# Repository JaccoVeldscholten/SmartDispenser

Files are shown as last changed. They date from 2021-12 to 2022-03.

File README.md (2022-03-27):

<div align="center">
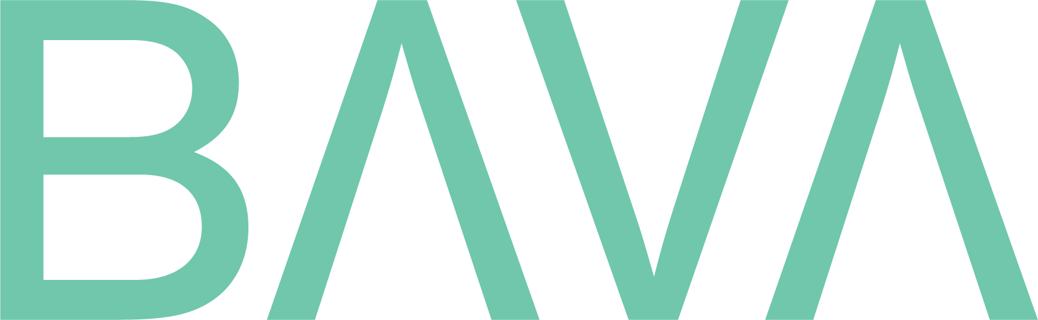
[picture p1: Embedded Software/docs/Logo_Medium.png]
  
</div>


![Build with PlatformIO](https://img.shields.io/badge/build%20with-PlatformIO-orange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)

# BAVA SmartDispenser 

Smart Dispenser is a device that has been developed to measure the odor in a toilet. If the smell of the toilet is of poor quality, a diffuser will be activated to dispel or mask the bad smell.

Measuring stench is done by a TVOC sensor. Furthermore, information is collected such as the temperature, moisture and how much the toilet is used.

## Installation

#### Windows (Tested on Windows 11)
* [Visual Code](https://code.visualstudio.com/) as IDE 
* [PlatformIO for code](https://platformio.org/install/ide?install=vscode) as extension for building on ESP32
* [SolidWorks](https://www.solidworks.com/) for editing the housing

After installing these tools the project can be pulled from GitHub and opened in VSCode and compiled & flashed with PlatformIO

## Usage / compiling
Please refer to [instructions](https://docs.platformio.org/en/latest/core/quickstart.html) of PlatformIO

For adjusting standard data see the chapter configuration.

## Configuration & Enviroment Variables
Many settings can be adjusted via the file config.h. Here are the WiFi settings and more relevant values.

It is also possible to set the threshold here when the sensor should be activated. The average value in a toilet is indicated in the table below. Certain values may differ per toilet. These are therefore adjustable in the configuration file.

| Measurement Value | No Lingering smell | Middle Lingering smell  | No Lingering smell | 
| :---: | :-: | :-: | :-: |
| TVOC PPM | 0 | 10 | > 10
| TVOC CO2 | 150 | 250 | > 250

More information and access to sample data can be seen in the Google Colab.

***Config.h***
````
/* WiFi Settings */
#define WIFI_SSID                       "TestSSID"
#define WIFI_PASSWORD                   "TestPassword!"

/* Defines the Min/Max Treshold of Stench in TVOC value */
#define TRESHOLD_PPM_MIN                3
#define TRESHOLD_PPM_MAX                5

/* Defines the Min/Max Treshold of Stench in CO2 value */
#define TRESHOLD_CO2_MIN                200
#define TRESHOLD_CO2_MAX                500

/* Measurement Interval */
#define TIME_TO_SLEEP          60     /* Time Device will go to sleep (in seconds) */            
#define TIME_TO_SLEEP_RECHECK  60     /* Time Device will go to sleep (in seconds) before recheck if someone left the toilet */
````

## Circuit Board
In order to combine the product into one product, it was decided to develop a printed circuit board containing the required sensors on board. Also, the microcontroller is soldered to the printed circuit board. More documentation about this object can be found at ....

## 3D Model & Assembly
The entire product is drawn in SolidWorks. The drawing files are included in this GitHub. A simple but handy model was taken into account because the model had to be printed with a 3D printer.

## Testing
The product has been extensively tested by data analyzes and used traceability matrixses to test the product. The results are included in this repo.

## Documentation in depth
Use the DoxyGen Folder for documentation.
For Writing Documentation use the following link: 

## License
MIT

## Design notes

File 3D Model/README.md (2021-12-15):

<div align="center">
  
</div>

# 3D Design & Assembly
To assemble the product, this page has been prepared for the developer or production employee to assemble the product together.

# Build instructions
***UNDER CONSTRUCTION**: This section will include:*
- *Bill of Materials*
- *Mechanical assembly instructions*
- *Electronics/Wiring instructions*

---

## Bill of materials
### 3D Printable
3D Printable files are found in [/CAD/3D Models (To Print)](../STL)
- [Base](../STL/Base.STL)
- [Backplate](../STL/Base.STL)
- [Battery Box](../STL/Base.STL)
- [Water Compartment](../STL/Base.STL)

*Optional*
- [Logo](../STL/Base.STL)
- [Box Design](../STL/Base.STL)
### Non 3D Printable
Some parts such as the mechanical parts or electrical parts cannot be printed. These must be purchased. The printed circuit board can be developed yourself. Read the Circuit Board section for this. The purchase of the printed circuit board can be done at BAVA Solutions.

### Electronic components
- **Circuit Board** Provider by BAVA Solutions (Or see Circuit Board Section)
- **TVOC Sensor** Sensor CCS811
- **Temperature Sensor** Bosch BME280 
- **Battery** 1S LiPo Aprox 3200 mAh

### Mechanical components
- **1x** Hot Glue Gun with sticks 

---

# Mechanical assembly

### Step 1: Print the base element
push fit the bearings and secure with a nut and bolt Push fit bearings

  The first step of assembly is to print the [base](../STL/Base.stl) element of the product. From this object it is possible to connect the rest of the elements.
  Print the basic element and lay it flat on the table with the open cloth outwards.<br><br><br><br><br><br><br><br><br>

---

### Step 2: Insert the water compartment 
push fit the bearings and secure with a nut and bolt Push fit bearings

  The first step of assembly is to print the [base](../STL/Base.stl) element of the product. From this object it is possible to connect the rest of the elements.
  Print the basic element and lay it flat on the table with the open cloth outwards.

---

### Step 3: Insert the sensors
push fit the bearings and secure with a nut and bolt Push fit bearings

  The first step of assembly is to print the [base](../STL/Base.stl) element of the product. From this object it is possible to connect the rest of the elements.
  Print the basic element and lay it flat on the table with the open cloth outwards.

---

### Step 4: Inert the circuit board
push fit the bearings and secure with a nut and bolt Push fit bearings

  The first step of assembly is to print the [base](../STL/Base.stl) element of the product. From this object it is possible to connect the rest of the elements.
  Print the basic element and lay it flat on the table with the open cloth outwards.

---

### Step 5: Connect the wires
push fit the bearings and secure with a nut and bolt Push fit bearings

  The first step of assembly is to print the [base](../STL/Base.stl) element of the product. From this object it is possible to connect the rest of the elements.
  Print the basic element and lay it flat on the table with the open cloth outwards.

---

### Step 6: Insert the battery
push fit the bearings and secure with a nut and bolt Push fit bearings

  The first step of assembly is to print the [base](../STL/Base.stl) element of the product. From this object it is possible to connect the rest of the elements.
  Print the basic element and lay it flat on the table with the open cloth outwards.

---

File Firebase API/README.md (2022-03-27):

## Index

[Overview API](#overview-api)

[Run Locally](#run-locally)

[Documentation](#documentation)

- ###### [AddDevice](#adddevice-1)
- ###### [AddDeviceData](#adddevicedata-1)
- ###### [AddLocation](#addlocation-1)
- ###### [GetAllBuildings](#getallbuildings-1)
- ###### [GetDeviceStatusPerBuilding](#getdevicestatusperbuilding-1)
- ###### [GetLogsOfADevice](#getlogsofadevice-1)
- ###### [GetStatsOfADevice](#getstatsofadevice-1)
- ###### [RemoveDevice](#removedevice-1)
- ###### [RemoveLocation](#removelocation-1)

[Deployment](#deployment)

[FAQ](#faq)

## Overview API

The API is hosted on Firebase functions. We choose for Firebase because we can also use Firebase Firestore as our document-based-database. Besides you pay for what you use. So if you don’t have a lot of customers you will not do a lot of requests to Firebase which means the costs for the API will also be low. As you can see in the image below there is even a free quota. So for development we don’t

With this API you can interact with the data which is generated by the smart dispensers.
You can also use our app which has the API integrated.

## Run Locally

Clone the project

```bash
  git clone git@gitlab.com:bava-solutions/bava-solutions-api.git
```

Go to the project directory

```bash
  cd bava-solutions-api
```

Install dependencies

```bash
  cd functions
  npm install
  npm install firebase-tools -g
  npm install nodemon -g
```

Start the server

```bash
  cd functions (if youre not already there)
  nodemon -e ts --exec "npm run serve"
```

## Documentation

In production environment the url for the api is "https://us-central1-bava-solutions.cloudfunctions.net/"
In development environment the url for the api is "http://localhost:5001/bava-solutions/us-central1/"

### AddDevice

POST `url/AddDevice`

| **Parameter** | **Type** | **Explanation** |
| --- | --- | --- |
| building | String | The name of the building you want to add. |
| gender | Number | 0 = both genders. 1 = male. 2 = female. |
| name | String | This is the name of the smartdispenser. |
| mac | String | This is the macaddress of the smartdispenser. |
| description | String | This is a description of the smartdispenser. |
| location | String | The location where the smartdispenser is located. |

Possible return code with data
```
StatusCode 315:
    "Please send a POST request"
StatusCode 404:
    "No building found with the name of {building}"
StatusCode 400:
{
    "err": error
}
StatusCode 200:
    "Device succesfully added!"
```

### AddDeviceData

POST `url/AddDeviceData`

| **Parameter** | **Type** | **Explanation** |
| --- | --- | --- |
| tvoc\_ppm | Number | This is the measured air quality |
| tvoc\_co2 | Number | This is the meusured CO2 that’s in the air |
| temp | Number | This is the temperature that the sensor of the smart dispenser measures. |
| hum | Number | This is the humidity that is measured |
| occupied | Boolean  | This variable will be true if someone is using the toilet. If the toilet is not occupied it will be false. |
| mac | String | This is the mac-address of the smart dispenser. |
| pressure | Number | This is the measured pressure in the air. |
| altitude | Number | This will be submitted because we want to check if the altitude has some impact on the other values. |
| liquidLevel | Number | This is a percentage of the amount of liquid left in the smartdispenser. |
| batteryLevel  | Number | This is a percentage of energy still left in the battery. |

Possible return codes with data
```
StatusCode 315:
    "Please send a POST request"
StatusCode 400:
{
    "err": error
}
StatusCode 400:
{
    "Temperature too high. Log aborted"
}
StatusCode 200:
    "Sensordata successful submitted"
```

### AddLocation

POST `url/AddLocation`

| **Parameter** | **Type** | **Explanation** |
| --- | --- | --- |
| buildingName  | String | This is the name of the building you want to add |
| companyName | String | This is the company of the building |
| address | String | This is the address of the building |

Possible return codes with data
```
StatusCode 315:
    "Please send a POST request"
StatusCode 400:
{
    "err": error
}
StatusCode 200:
    "Location successful added"
```

### GetAllBuildings

GET `url/GetAllBuildings`

Possible return code with data
```
StatusCode 400:
{
    "err": error
}
StatusCode 200:
[
    "Chef",
    "Fokke",
    "Hanz",
    "BuildingGoogle"
]

```

### GetDeviceStatusPerBuilding

in the place of `MACADDRES` you need to put the macaddress

GET `url/GetDeviceStatusPerBuilding/MACADDRES`

Possible return code with data
```
StatusCode 404:
    "No building found with the name of {BUILDING}"
StatusCode 404:
    "No devices connected to building {BUILDING}"
StatusCode 400:
{
    "err": error
}
StatusCode 200:
[
  {
    "mac": "F0:08:D1:D8:07:D4",
    "altitude": 142,
    "tvoc_ppm": 8,
    "tvoc_co2": 198,
    "liquidLevel": 100,
    "timestamp": {
      "_seconds": 1638423192,
      "_nanoseconds": 216000000
    },
    "pressure": 99682,
    "hum": 36,
    "batteryLevel": 100,
    "occupied": true,
    "temp": 19,
    "name": "real device",
    "location": "Jacco WC",
    "description": "pls dont delete",
    "gender": 0
  }
]
```

### GetLogsOfADevice

in the place of `MACADDRES` you need to put the macaddress

GET `url/GetLogsOfADevice/MACADDRES`

Possible return code with data
```
StatusCode 400:
{
    "err": error
}
StatusCode 200:
[
  {
    "tvoc_co2": 0,
    "hum": 40,
    "batteryLevel": 100,
    "occupied": true,
    "temp": 23,
    "liquidLevel": 100,
    "timestamp": {
      "_seconds": 1638397086,
      "_nanoseconds": 712000000
    },
    "altitude": 160,
    "pressure": 99477,
    "mac": "F0:08:D1:D8:07:D4",
    "tvoc_ppm": 0
  },
  {
    "tvoc_co2": 179,
    "batteryLevel": 100,
    "hum": 40,
    "mac": "F0:08:D1:D8:07:D4",
    "temp": 23,
    "timestamp": {
      "_seconds": 1638397235,
      "_nanoseconds": 972000000
    },
    "pressure": 99480,
    "altitude": 160,
    "liquidLevel": 100,
    "tvoc_ppm": 5,
    "occupied": true
  }
]
```

### GetStatsOfADevice

in the place of `MACADDRES` you need to put the macaddress

GET `url/GetStatsOfADevice/MACADDRES`

Possible return code with data
```
StatusCode 400:
{
    "err": error
}
StatusCode 200:
{
    "TotalVisitors": {
    "01/12/2021": 7,
    "02/12/2021": 58,
    "03/12/2021": 29
    },
    "AverageTemperature": {
    "01/12/2021": 22.04,
    "02/12/2021": 21.589041095890412,
    "03/12/2021": 18.8796992481203
    },
    "AverageHumidity": {
    "01/12/2021": 39.28,
    "02/12/2021": 32.10502283105023,
    "03/12/2021": 30.60902255639098
    },
    "Last100MeasuredPPM": {
    "01:42": 6,
    "01:47": 8,
    "01:52": 7,
    "01:57": 7,
    }
}
```

### RemoveDevice

POST `api/RemoveDevice`

| **Parameter** | **Type** | **Explanation** |
| --- | --- | --- |
| building | String | The name of the building you want to delete.  |
| mac | String | This is the macaddress of the smartdispenser. |

Possible return code with data
```
StatusCode 315:
    "Please send a POST request"
StatusCode 404:
    "No building found with the name of {building}"
StatusCode 400:
{
    "err": error
}
StatusCode 200:
    "Device succesfully removed!"
```

### RemoveLocation

POST `url/RemoveLocation`

| **Parameter** | **Type** | **Explanation** |
| --- | --- | --- |
| buildingName  | String | The name of the building you want to delete |

Possible return code with data
```
StatusCode 315:
    "Please send a POST request"
StatusCode 400:
{
    "err": error
}
StatusCode 200:
    "Gebouw {buildingName} verwijderd"

```
## Deployment

To deploy this project run the following commands inside your project directory

```bash
  cd functions
  npm run deploy
```

## FAQ

#### How do I use this API?

You can call the endpoints from the production environment.
There is also an example app with implementation for the API available on our Git.

#### Is the API free to use?

Yes, however in the future there might be some new functions which will be hidden behind a paywall

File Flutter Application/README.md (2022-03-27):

# bava

A new Flutter project.

## Getting Started

FlutterFlow projects are built to run on the Flutter _stable_ release.

### IMPORTANT:

For projects with Firestore integration, you must first run the following commands to ensure the project compiles:

```
flutter pub get
flutter packages pub run build_runner build --delete-conflicting-outputs
```

This command creates the generated files that parse each Record from Firestore into a schema object.

### Getting started continued:

This project is a starting point for a Flutter application.

A few resources to get you started if this is your first Flutter project:

- [Lab: Write your first Flutter app](https://flutter.dev/docs/get-started/codelab)
- [Cookbook: Useful Flutter samples](https://flutter.dev/docs/cookbook)

For help getting started with Flutter, view our
[online documentation](https://flutter.dev/docs), which offers tutorials,
samples, guidance on mobile development, and a full API reference.

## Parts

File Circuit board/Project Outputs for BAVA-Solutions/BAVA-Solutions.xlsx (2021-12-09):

Comment | Description | Designator | Footprint | LibRef | Quantity
10uF | Chip Multilayer Ceramic Capacitors for General Purpose, 0603, 10uF, X5R, 15%, 20%, 6.3V | C1, C2, C8 | FP-GRM188-0_1-e0_2_0_55-IPC_C | CMP-2006-02792-2 | 3
100nF | Chip Capacitor, 0.1 uF, +/- 10%, 50 V, -55 to 125 degC, 0603 (1608 Metric), RoHS, Tape and Reel | C3, C4, C5, C6, C7 | CAPC1608X90X35ML10T15 | CMP-2100-03643-1 | 5
BAT54HT1G | Schottky Barrier Diode, 2-Pin SOD-323, Pb-Free, Tape and Reel | D1 | ONSC-SOD-323-2-477-02_V | CMP-1055-00462-1 | 1
B2B-XH-A(LF)(SN) | CONN HEADER VERT 2POS 2.5MM | J1, J4 | FP-B2B-XH-A_LF_SN-MFG | CMP-2000-05888-3 | 2
B3B-XH-A(LF)(SN) | CONN HEADER VERT 3POS 2.5MM | J2, J5 | FP-B3B-XH-A_LF_SN-MFG | CMP-17439-000014-2 | 2
629105150921 | Micro USB 2.0 Type AB Receptacle WR-COM, Horizontal, SMT | J3 | 629105150921 | CMP-1502-03249-1 | 1
S6B-XH-A-1(LF)(SN) | CONN HEADER R/A P6OS 2.5MM | J? | FP-S6B-XH-A-1_LF_SN-MFG | CMP-17439-000023-1 | 1
ESP32-WROOM-32D | WIFI MODULE 32MBITS SPI FLASH | MD1 | FP-ESP32-WROOM-32D-MFG | CMP-194065-000003-1 | 1
61301011121 | THT Vertical Pin Header WR-PHD, Pitch 2.54 mm, Single Row, 10 pins | P1 | 61301011121 | CMP-1502-01082-1 | 1
NPN | High Voltage Transistor, NPN Silicon, 3-Pin SOT-23, Pb-Free, Tape and Reel | Q1, Q2 | ONSC-SOT-23-3-318-08_V | CMP-1048-00662-1 | 2
MMBT2222ALT1G | General Purpose Transistor, NPN Silicon, 3-Pin SOT-23, Pb-Free, Tape and Reel | Q3 | ONSC-SOT-23-3-318-08_V | CMP-1048-00538-1 | 1
10K | Chip Resistor, 10 KOhm, +/- 1%, 0.1 W, -55 to 155 degC, 0603 (1608 Metric), RoHS, Tape and Reel | R1, R4, R5, R6, R7, R8, R11 | RESC1609X55X30LL15T15 | CMP-1012-00623-3 | 7
470 | Chip Resistor, 10 KOhm, +/- 1%, 0.1 W, -55 to 155 degC, 0603 (1608 Metric), RoHS, Tape and Reel | R2, R3 | RESC1609X55X30LL15T15 | CMP-1012-00623-3 | 2
1K | Chip Resistor, 10 KOhm, +/- 1%, 0.1 W, -55 to 155 degC, 0603 (1608 Metric), RoHS, Tape and Reel | R10 | RESC1609X55X30LL15T15 | CMP-1012-00623-3 | 1
1571527-2 | SWITCH TACTILE SPST-NO 0.05A 24V | SW1, SW2 | FP-1571527-2-MFG | CMP-03402-000033-1 | 2
TC1262-3.3VDBTR | 500mA Fixed Output CMOS LDO, 3-Pin SOT-223, Extended Temperature, Tape and Reel | U1 | SOT-223-DB3_L | CMP-0136-00481-1 | 1
CH340C | USB to serial chip CH340 | U2 | SO016 | CH340C | 1
BME280 | SENSOR PRESSURE HUMIDITY TEMP | U3 | FP-BME280-MFG | CMP-2000-05073-3 | 1
1655 | Intelligent Control LED Integrated Light Source, 3.5 to 5.3 V, -25 to 80 degC, 4-Pin SMD, RoHS, Tape and Reel | U4 | ADA-RGB-1655_V | CMP-2000-05026-1 | 1

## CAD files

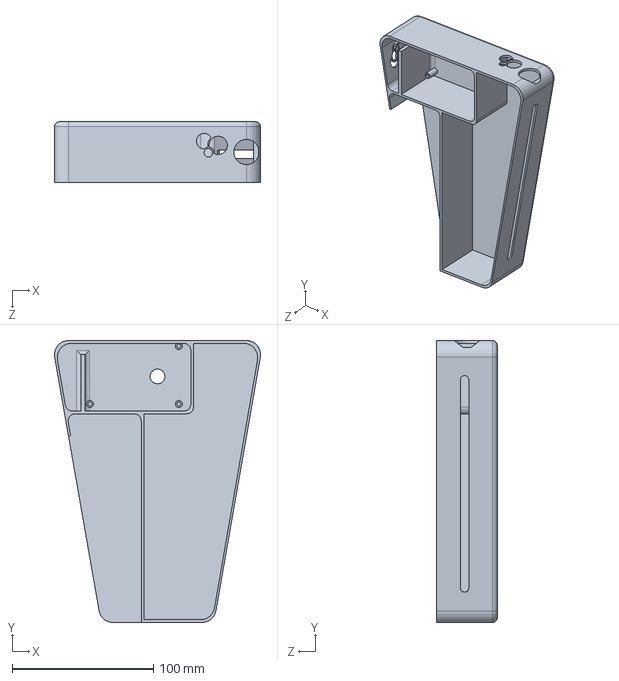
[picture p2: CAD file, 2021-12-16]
3D Model/New_front.SLDPRT
146.1 x 200.0 x 43.0 mm

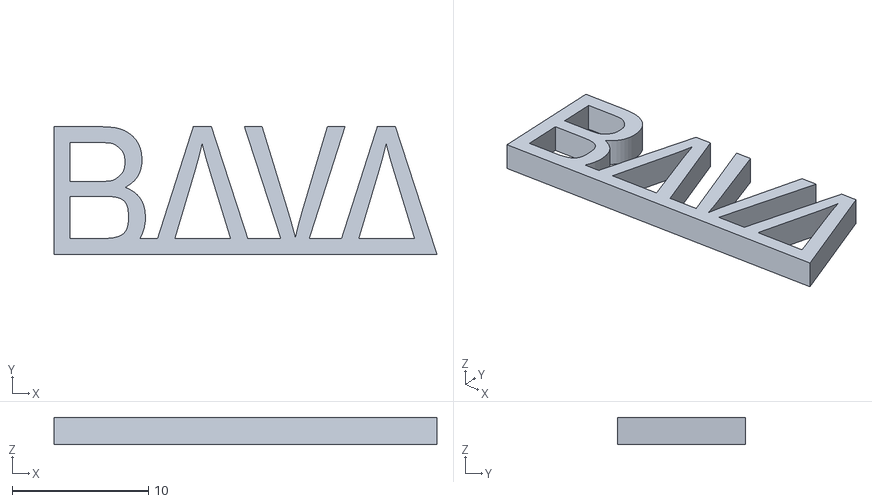
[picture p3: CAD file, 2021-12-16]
3D Model/STL/Logo.STL
28.1 x 9.36 x 2.00

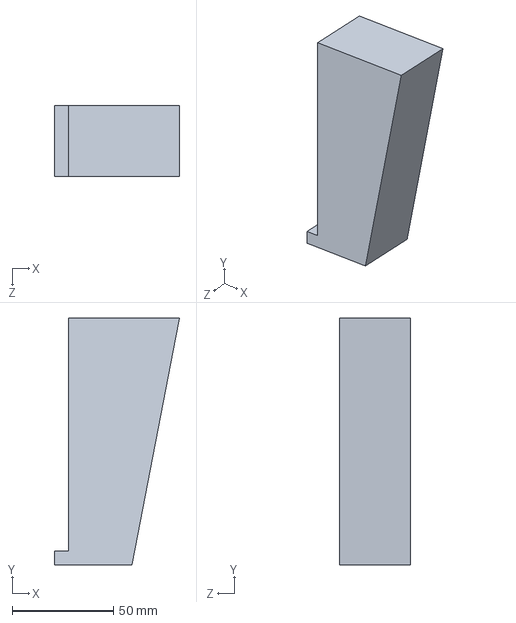
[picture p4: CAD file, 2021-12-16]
3D Model/Real_Water.SLDPRT
61.8 x 122.0 x 35.0 mm

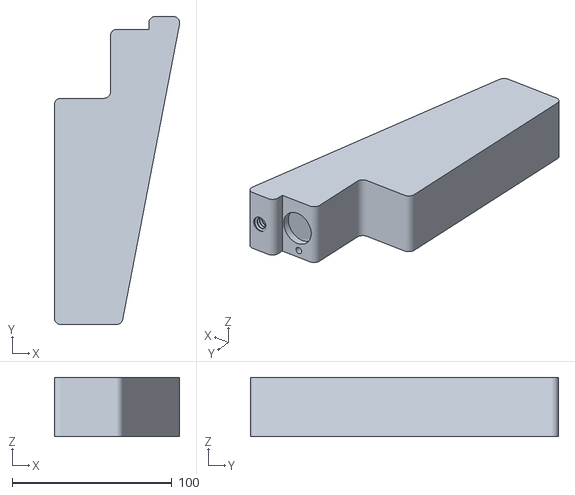
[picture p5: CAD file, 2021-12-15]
3D Model/STL/Water Compartment.STL
78.6 x 193.0 x 37.0

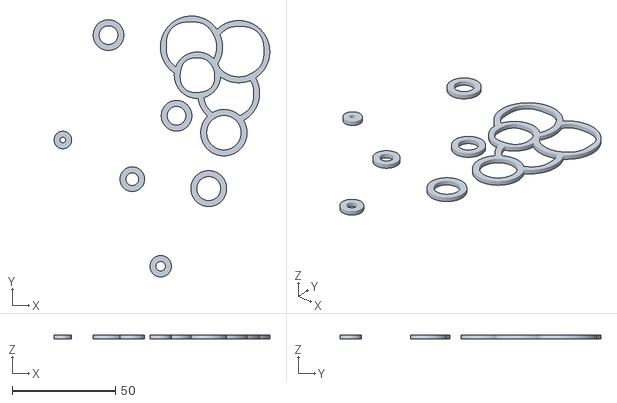
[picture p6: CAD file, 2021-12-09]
3D Model/STL/Front Design.STL
104.7 x 126.6 x 2.00

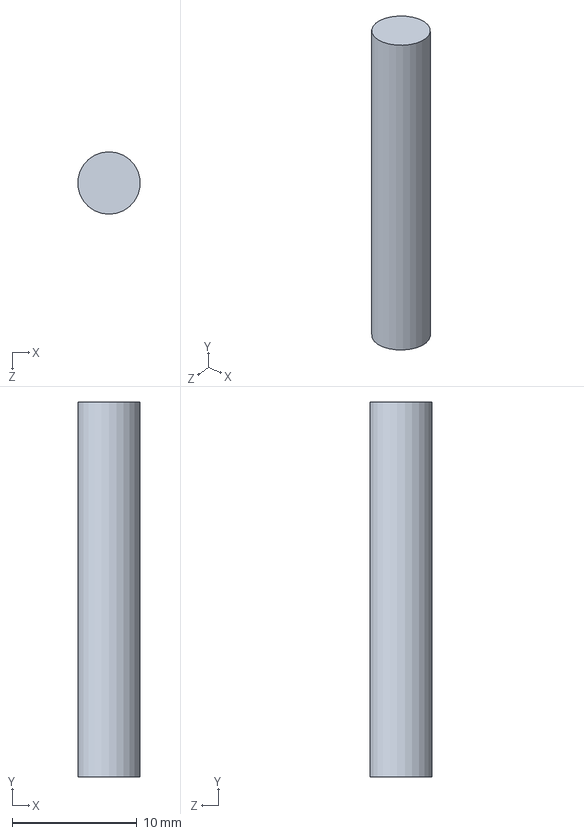
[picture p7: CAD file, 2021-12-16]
3D Model/Cotton_Stick.SLDPRT
4.96 x 30.0 x 5.00 mm

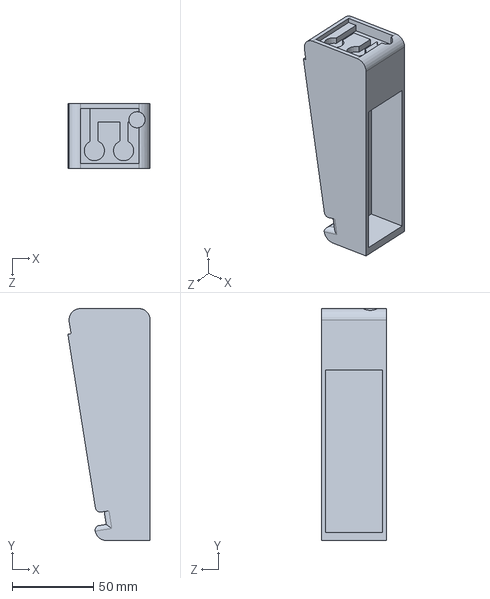
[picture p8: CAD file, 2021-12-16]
3D Model/Battery_Box.SLDPRT
50.7 x 143.0 x 40.0 mm

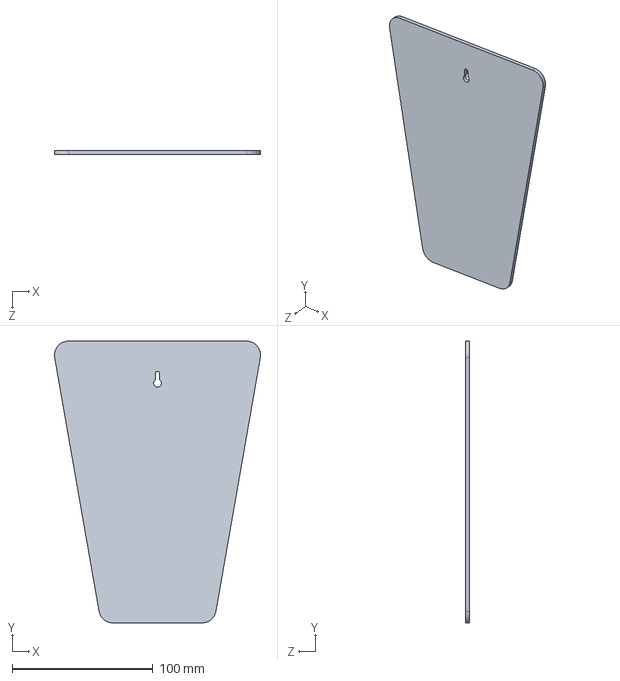
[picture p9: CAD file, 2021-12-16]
3D Model/BackPlate.SLDPRT
146.1 x 200.0 x 3.01 mm

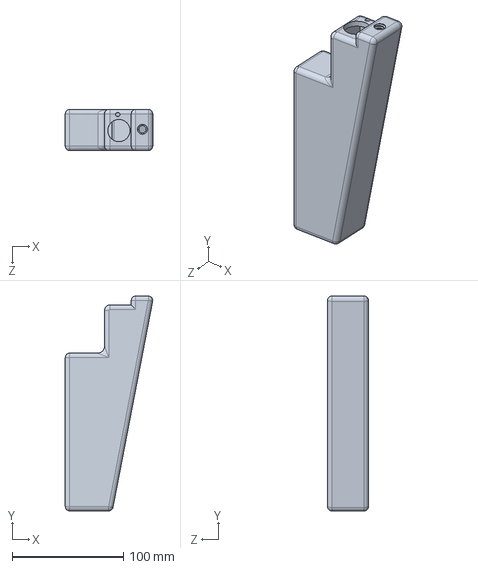
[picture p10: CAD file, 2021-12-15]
3D Model/New_Water_Comp_Bottom_Without.SLDPRT
78.6 x 193.0 x 37.0 mm

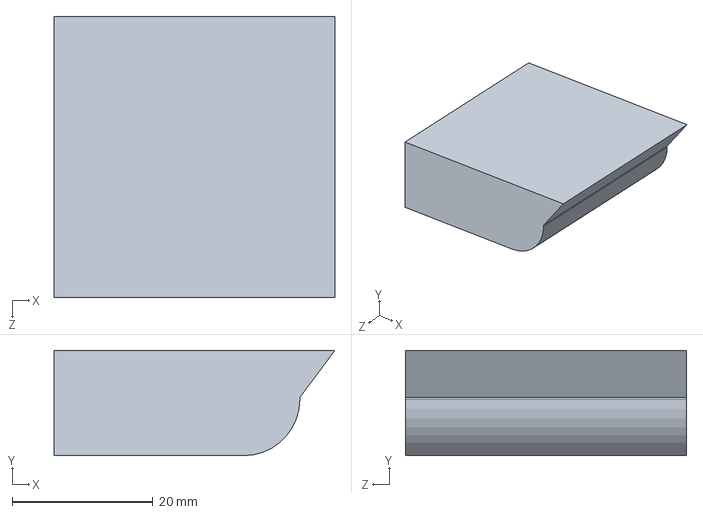
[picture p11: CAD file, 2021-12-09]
3D Model/Sponge.SLDPRT
40.0 x 15.0 x 40.0 mm

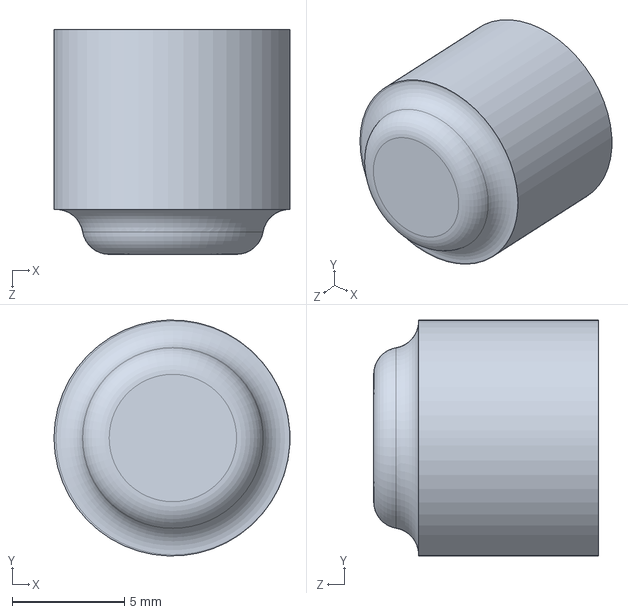
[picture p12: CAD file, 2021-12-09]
3D Model/Motion_Detector.SLDPRT
10.5 x 10.5 x 10.0 mm

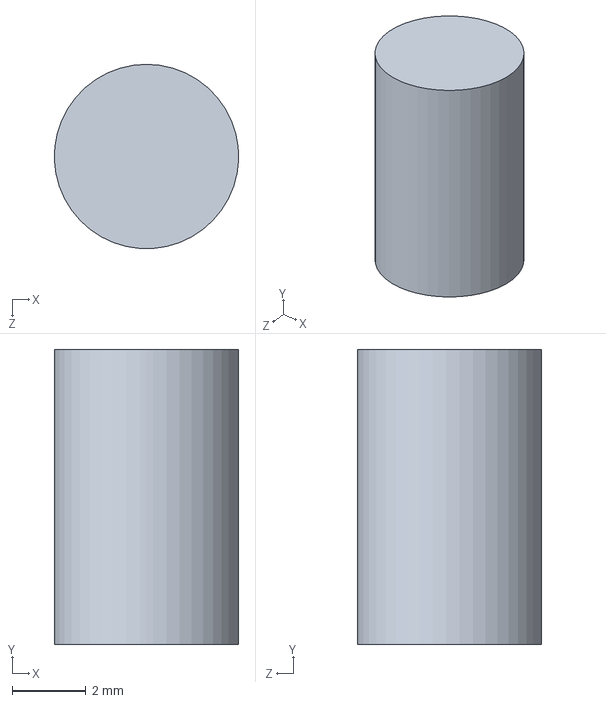
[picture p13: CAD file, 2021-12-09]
3D Model/Cotton_Stick_Small.SLDPRT
5.00 x 8.00 x 5.00 mm

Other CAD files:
3D Model/New_Water_Comp_Bottom_With.SLDPRT
3D Model/STL/Base.STL
3D Model/Front_Plate_Logo.SLDPRT
3D Model/Front_Plate_Circles.SLDPRT
3D Model/STL/BackPlate.STL
3D Model/STL/Battery Box.STL
3D Model/STL/Front_Plate_Logo.STL

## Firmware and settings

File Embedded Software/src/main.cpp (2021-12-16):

#include <Arduino.h>
#include <WiFi.h>
#include <TVOC.h>
#include <Uplink.h>
#include <BME280.h>
#include <Temperature.h>
#include "driver/gpio.h"
#include <esp_wifi.h>

#include "config.h"


typedef enum STATE
/** Enum type for StateMachine. 
 *  A state machine is used to avoid errors. 
 *  Because a state is fixed, it is not possible to simply call in a wrong state.
 *  There are mulitple states mentioned.
*/
{
  MAIN,                   /**<  Main state */
  DIFFUSING,              /**<  Difussing state */
  PERSON_ENTERED,         /**<  Someone entered the toilet state*/
  FAILURE                 /**<  In case something went wrong */
} State;

TVOC tvoc;                                /*!< Constructor for the TVOC Sensor */
Uplink server;                            /*!< Constructor for the Uplink Server */
Temperature temp;                         /*!< Constructor for the Temperature & Humidty sensor*/

RTC_DATA_ATTR int bootCount = 0;         /*!< RCC Data Adress being used to keep this variable after deep sleep */
RTC_DATA_ATTR State state;               /*!< RCC Data Adress being used to keep this variable after deep sleep */
RTC_DATA_ATTR bool checkSum = false;     /*!< RCC Data Adress being used to keep this variable after deep sleep */



void UploadData(void);
void CheckAirQuality(void);
void SelectWakeUp(void);
void setup(void);


void UploadData(void)
{
  /**
  * 
  * This function will fetch all the sensor values and arrange them in JSON format
  * 
  * After this the files will be send to "Uplink class" to proceed uploading
  * 
  * @warning Waterlevel & batteryLevel are not implemented yet
  */
  server.doc["tvoc_ppm"] = tvoc.fetchTVOC();
  server.doc["tvoc_co2"] = tvoc.fetchC02();
  server.doc["temp"] = temp.fetchTemp();
  server.doc["hum"] = temp.fetchHum();
  server.doc["occupied"] = (state == PERSON_ENTERED) ? true : false;
  server.doc["pressure"] = temp.fetchPressure();
  server.doc["altitude"] = temp.fetchAltitude();
  server.doc["liquidLevel"] = 100;
  server.doc["batteryLevel"] = 100;
  // Mac Adress is added in function SendData  server.doc["mac"]

  server.SendData();
}


void CheckAirQuality(void){

  /**
  * 
  * This function will check if the values of the stench are high (TVOC)
  * 
  * In case the TVOC values are between setted Treshholds the state DIFFUSING is kicked in.
  * 
  * @note The tresholds are able to change in "config.h"
  */
  if ((tvoc.fetchTVOC() >= TRESHOLD_PPM_MIN) && (tvoc.fetchTVOC() <= TRESHOLD_PPM_MAX) ){
      Serial.println("It stinks");
      state = DIFFUSING;
  }
}


void SelectWakeUp(void)
{
  /**
  * When the device wakes up after sleep this function will check waht sleep mode it came from.
  * In this way its possible to set the state caused by someone that entered the toilet.
  */
  switch (esp_sleep_get_wakeup_cause())
  {
  case 2:
    Serial.println("Wakeup caused by PIR");
    state = PERSON_ENTERED;
    break;
  case 4:
    Serial.println("Wakeup caused by timer");
    break;
  default:
    Serial.println("Wakeup was not caused by something else");
    break;
  }
}

void setup()
{
  Serial.begin(DEBUG_BAUD);
  sys_delay_ms(100);                                    /* Give the Bus some time to setup */
  bootCount++;                                          /* Keep track of the boot time */
  Serial.println("Boot number: " + String(bootCount));
  Serial.println("We are coming in with state: " + String(state));
  SelectWakeUp();

  pinMode(GPIO_MOTION_PIR, INPUT);

  server.APIUrl = API_URL; // Parse config

  /* Init the sensors without spamming the I2C bus */
  /* The delay also helps to give the TVOC Sensor time to measure */
  tvoc.initSensor();
  sys_delay_ms(250);
  temp.initSensor();
  sys_delay_ms(250);

  Serial.println("Setup wifi Begin\n");
  WiFi.disconnect();
  WiFi.begin(WIFI_SSID, WIFI_PASSWORD);
  
  uint8_t wifiTimout = 0;
  while (WiFi.status() != WL_CONNECTED)
  {
    Serial.print('.');
    delay(1000);
    /* In case the WiFi is still not connected the MCU will restart */
    if(wifiTimout++ > WIFI_TIMER_TRESHOLD){
      ESP.restart();
    }
  }
  Serial.println();
  Serial.println("Connected!");

  Serial.println(digitalRead(GPIO_MOTION_PIR));
  if ((!digitalRead(GPIO_MOTION_PIR)) && (state == PERSON_ENTERED) && (checkSum))
  {
    /**
     * **Person Left Toilet State**
     * 
     * This state is activated when the current Timer (2 min, configureable in "config.h") is triggerd.
     * Another condition is that the value of the motion detector must be 0. (No Motion) 
     * 
     * First, the data is uploaded to the server.
     * After that, a measurement is started to see if there is any stench in the toilet.
     * Then all interrupts are activated again.
     * 
     * Finally, the state of the device is set back to main.
     * 
     * @note variable checkSum is being used to prevent to join the state again if the person is not left yet.
     */
    checkSum = false;
    state = MAIN;
    UploadData();
    esp_sleep_enable_timer_wakeup(TIME_TO_SLEEP * uS_TO_S_FACTOR );
    esp_sleep_enable_ext0_wakeup(GPIO_NUM_14, 1);
    Serial.println("\nPERSON LEFT TOILET (Sleep 10 min now)");
  }

  if(digitalRead(GPIO_MOTION_PIR) && (state == PERSON_ENTERED) && (checkSum)){
    /**
     * **Person Still on Toilet State**
     * 
     * This state is activated when the current Timer (2 min, configureable in "config.h") is triggerd.
     * Another condition is that the value of the motion detector must be 1. (Still Motion) 
     * 
     * This state is very clear. Just bring the device back in sleep mode. And check in 2 min again :)
     * 
     * @note variable checkSum is being used to prevent to join the state again if the person is not left yet.
     */
    Serial.println("\nPERSON STILL ON TOILET (Sleep 2 min now)");
    esp_sleep_enable_timer_wakeup(TIME_TO_SLEEP_RECHECK * uS_TO_S_FACTOR );
  }

  if ((state == PERSON_ENTERED) && (!checkSum))
  {
    /**
     * **Person Entered Toilet State**
     * 
     * This state is activated when the Motion Detector (PIR) is triggerd.
     * After this the PIR Interrupt is being disabled.
     * 
     * The global interrupt timer is set to 2 min (Changable in "config.h") 
     * This timer will check every 2 min if the person left the toilet.
     * 
     * Finally, the data will be uploaded to the server. This will indicate that the toilet is occupied.
     * 
     * @note variable checkSum is being used to prevent to join the state again if the person is not left yet.
     */
    checkSum = true;
    esp_sleep_disable_wakeup_source(ESP_SLEEP_WAKEUP_EXT1);
    esp_sleep_enable_timer_wakeup(TIME_TO_SLEEP_RECHECK * uS_TO_S_FACTOR );
    UploadData();
    CheckAirQuality();
    Serial.println("\nPERSON ENTERED TOILET (Sleep 2 min now)");
  }

  if (state == MAIN)
  {
    /**
     * **Main Measurement State**
     * 
     * This state is triggered by a global timer that goes off every 10 minutes.
     * In this state, all interrupts are re-enabled just to be safe.
     * 
     * After this, a measurement is started to measure any stench. Then the data will be uploaded.
     * 
     */
    esp_sleep_enable_ext0_wakeup(GPIO_NUM_14, 1);
    esp_sleep_enable_timer_wakeup(TIME_TO_SLEEP * uS_TO_S_FACTOR);
    UploadData();
    Serial.println("\nIM IN THE MAIN STATE (Sleep 10 min now)");
  }
    
  esp_deep_sleep_start();   /* Every State Entry will result in sleep */
}

void loop(){}   /* The Loop is not being used */

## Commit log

2021-12-15 Updated Water comp
    [New_Water_Comp_Bottom.SLDPRT, New_Water_Comp_Bottom_With.SLDPRT, New_Water_Comp_Bottom_Without.SLDPRT]
2021-12-15 Water Comp update
    [New_Water_Comp_Bottom_With.SLDPRT, New_Water_Comp_Bottom_With.STL]
2021-12-16 Updated 3D Design
    [BackPlate.SLDPRT, BackPlate.STL, Logo.STL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]
2021-12-16 Updated 3D Files + Formatted code
    [Battery_Box.SLDPRT, Cotton_Stick.SLDPRT, New_Water_Comp_Bottom_With.SLDPRT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]
2021-12-17 Added logo STL
    [Front_Plate_Logo.STL]
